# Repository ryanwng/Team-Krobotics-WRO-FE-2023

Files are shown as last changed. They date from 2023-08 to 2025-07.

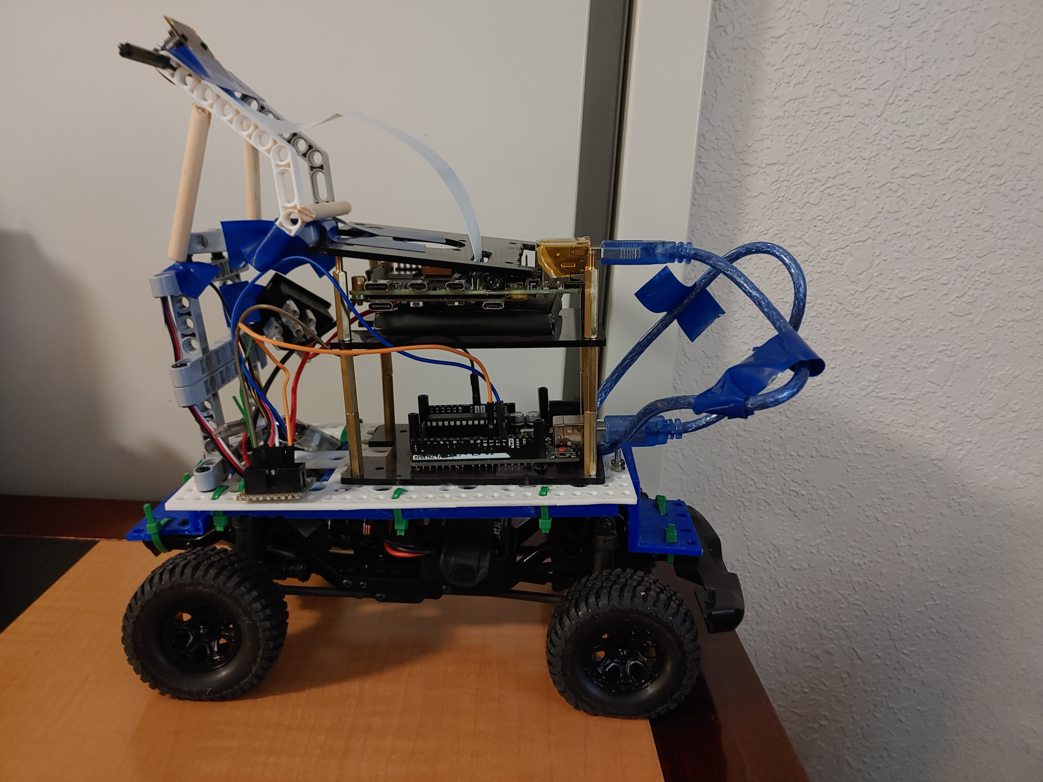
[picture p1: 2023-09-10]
v-photos/Left Side.jpg

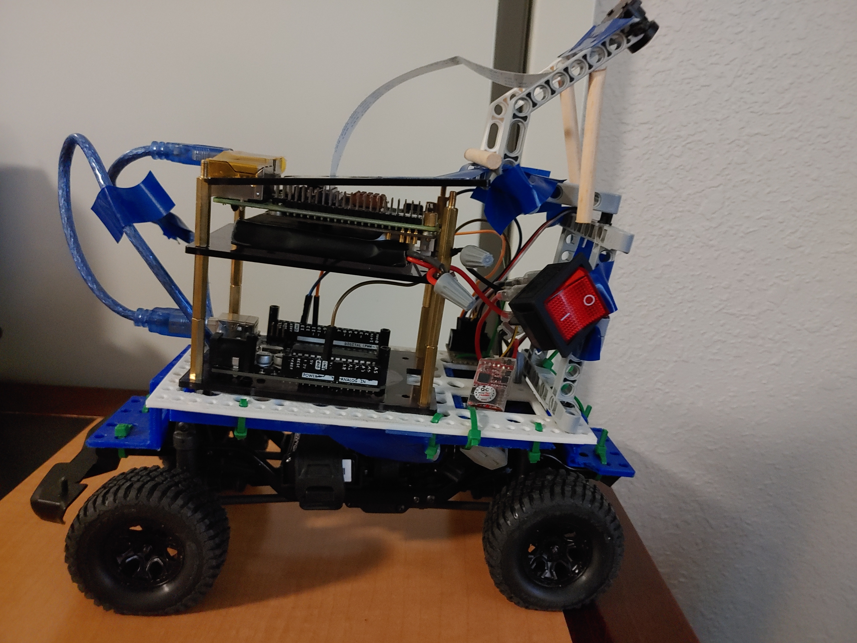
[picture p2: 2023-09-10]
v-photos/Right Side.jpg

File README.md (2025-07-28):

# WRO-FE-2023

# Engineering Documentation | Team Krobotics | Canada
----

This repository contains engineering materials of The Krobot, a vehicle's model from Team Krobotics, for the WRO Future Engineers competition for the 2023 season.

The theme "Connecting the World" focused on exploring how robots can improve shipping logistics and digial infrastuructre to promote safety, sustainability and efficiency. In the Future Engineers category, the competition was to design a self-driving autonomous robot vehicle which was capable of navigating around a randomly generated track with obstacles acting as "traffic lights."

----

## Team Members:

- Kevin Yang - email: kevin.yang.toronto@gmail.com
- Ryan Wang - email: wangryan833@gmail.com

----

## Repository Overview

models - contains 3D printable files for some parts of our robot

schemes - contains a schematic of the the electrical systems

src - contains the code for our robot

t-photos - contains team photos, one serious and one funny

v-photos - contains vehicle photos, from all directions

video - contains youtube links for videos of our robot

----

# Program arrangement and Algorithm Planning
The robot runs on a Raspberry Pi board, we also use an Arducam for Raspberry Pi Camera, OV5647 Pi Camera Module. It detects the surrounding environment including walls and red/green obstacles. The motor and steering servo are both connected to our Arduino Uno board. To count the number of laps, we see how many times the robot detects a low area of ROI one either side (which indicates when it turns). Once it reaches 12, we stop the program after a set amount of time.

When the robot is turned on, it will communicate with the Raspberry Pi, and then waits for a button to be pressed. Once the button is pressed, the servo motor is set to center and the motor speed is set to zero.

**Step 1 - Starting Run:**

We start by accelerating the motor, and begin in the wall-following state. We draw contours and calculate the area of the wall on either side. The difference between the areas is proportional to the distance from the car to the center of the lane.

**Step 2 - Avoiding Walls:**

We run a PID(proportional, integral, derivative) controller to complete the run and avoid the walls. The robot tries to stay in the center of the track by adjusting its position based on the areas of the walls. If the left area is larger, it will correct the error by turning to the right and vice versa. Once the walls’ area on one side is almost nothing, we turn towards that side because it means that it is open and thus we turn in that direction.

**Step 3 - Avoiding Obstacles**

In order to turn correctly for the traffic lights, we have a region of interest at the front of the car which can detect the blocks. We then use HSV values to only capture the blocks, and we find the x and y coordinates of the pillar. Then we adjust to the left and right according to the colour of the pillar, relative to the x-coordinate of the pillar. The y-coordinate of the pillar will dictate how steep of a turn will be needed in order to get to the desired x coordinate, which will in turn mean going around the pillar.

**Step 4 - Counting Laps**

As previously mentioned, the car counts the number of laps by the number of times the car detects lack of area in either left or right ROI. Once it counts that it has turned 12 times, it means that 3 laps have occurred. Then, the program will stop after 8 seconds to ensure it ends in the final area.

----

# Mechanical Parts

**Traxxas Trx4M**

The Traxxas Trx4m was initially chosen due to the fact that it would be easy to modify, as well as being a great all around car which is able to handle all sorts of terrain, electrical components being compatible with ours, as well as fitting the size and weight restraints of the car.

**Raspberry Pi 4 Model B**

The Raspberry Pi was chosen as it is a common computing device which allows for all sorts of coding and intricate use which will be helpful in the competition. Some examples will be communication with the arduino, attaching a camera and powersource, and using the vast amount of libraries that the pi has to offer.

**Arduino Uno R3**

The Arduino was chosen for its popularity and for its great synergy with the Raspberry Pi. Also, it allowed for easy control of the DC motor and the Servo motor, with an easy to understand programming interface and great debugging.

**Furitek Micro Komodo Motor**

The Furitek motor was used over the original Traxxas motor due to the fact that it was brushless versus the latter which was brushed. There are many benefits for using a brushless motor as opposed to a brushed motor. Brushless motors require less power, produce higher speed, and also make less noise.

**Traxxas LiPo Battery and charger**

The battery and charger which powers the DC and Servo motor. The only changes made were connections with the wiring.

**PiSugar S Pro**

The Raspberry Pi Sugar was used to power the Pi, which also ended up powering the Arduino. This would be important in ensuring that both the Pi and Arduino would have sufficient power to run at its full capacity. However, a slight issue occurred as we have two power sources, and the restraints made it such that we could only have one switch to turn both of them on. More will be discussed about this later in the DPST switch section.

**DPST Switch**

Due to the rules, it restricts us to having only one switch to fully turn on the robot. Due to the fact that we have both a power source for the Pi and Arduino, and a power source for the motors, it meant that these two connections had to be connected into one switch. This was done using the DPST switch.

**Mechanical Design**

We decided to use a Traxxas Trx4M as our base, the chassis was expanded on using 3D printed elements and zipties in order to ensure the stability of our parts. For example, our camera is stabilized on a 3D printed mount, which is stabilized through the use of glue and zipties. Our motor is a Furitek Micro Komodo Motor, it has 3 wires that connect to our esc to control speed and torque. This motor is directly compatible with the car we picked. Using cases and bases to hold the Raspberry Pi and its respective power source was helpful in condensing the robot in size. Lego was also used to create a camera stand to ensure that the camera would face down. Finally, tape was used in some areas, along with hot glue to increase the stability of the car in weaker areas.

**3D Parts**

A base was designed in order to hold the Raspberry Pi, Arduino, wiring and some other pieces. A camera stand was previously designed to ensure that the camera would stay in the same place and be stable while driving. However, it was figured later on that the camera wouldn't be able to face down, and so the stand was made with lego and some wooden pieces to ensure it would stay in place. 

**Hardware Issues**

There ended up being some hardware issues which he had to fix throughout the preparation of the competition. Firstly, the use of the button on the Pi Sugar S Pro was necessary in order to fulfill the requirements of the competition of using only one button to start the program. This meant adding additional code, along with solidfying the reason for using the Pi Sugar S Pro compared to other power sources, such as lithium batteries. Also, for the Raspberry Pi it would be necessary to code a way to run a program immediately upon turning on. This was done using the command "sudo crontab -e" which allows for programs to run upon rebooting of the raspberry pi. This alongside with the GPIO button on the Pi Sugar S pro was invaluable in allowing for a suitable car which can perform all its necessary functions.

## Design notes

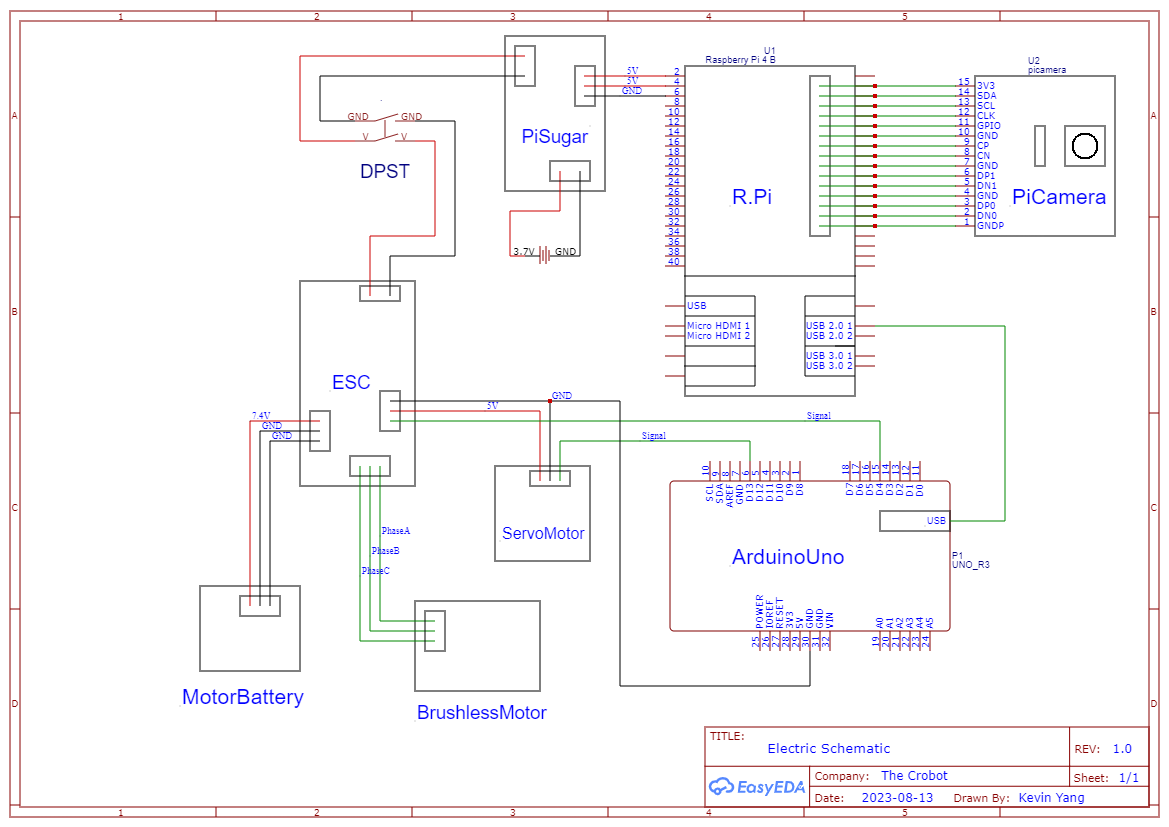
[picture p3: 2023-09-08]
schemes/Updated Electric Schematic.png

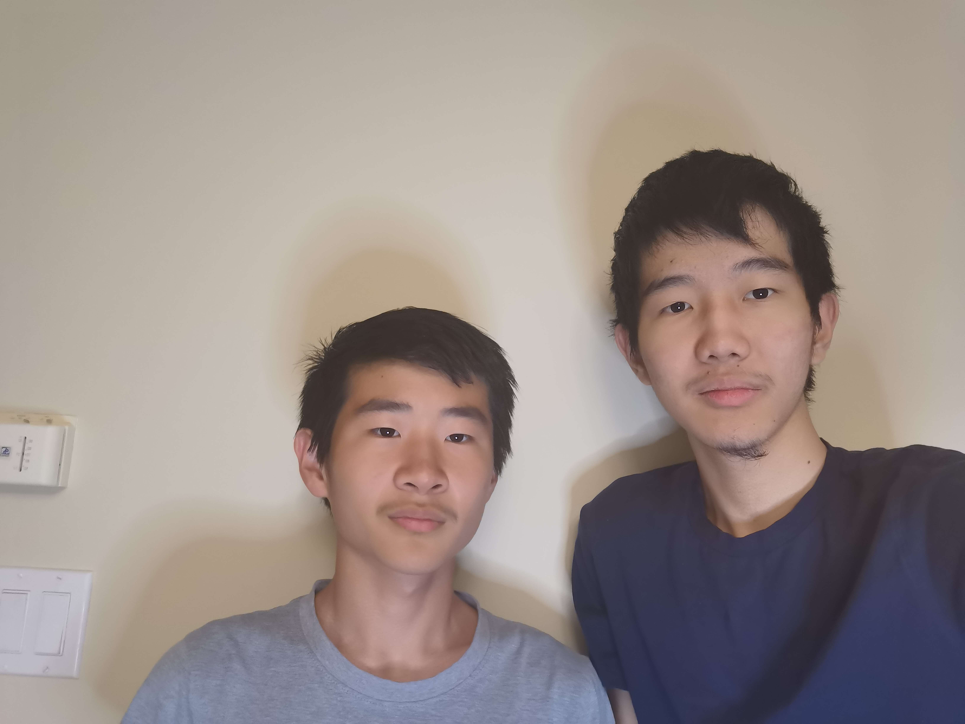
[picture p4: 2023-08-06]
t-photos/TeamPhoto.jpg

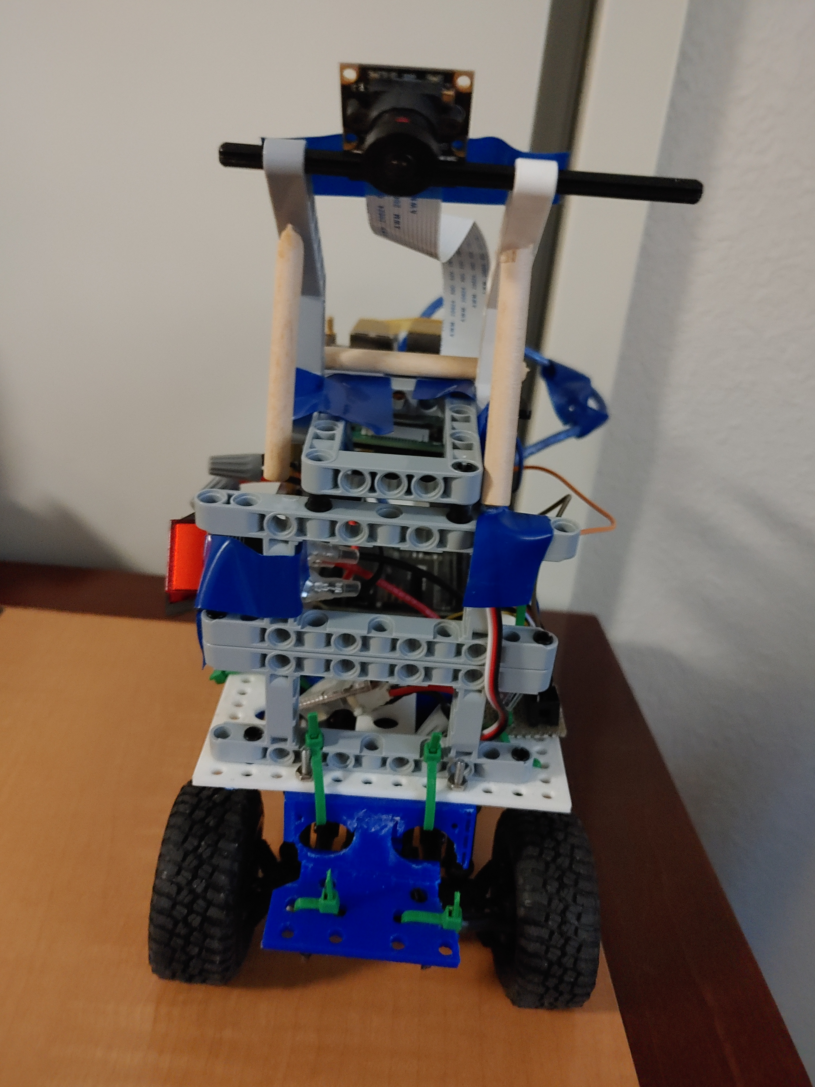
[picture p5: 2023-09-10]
v-photos/Front Side.jpg

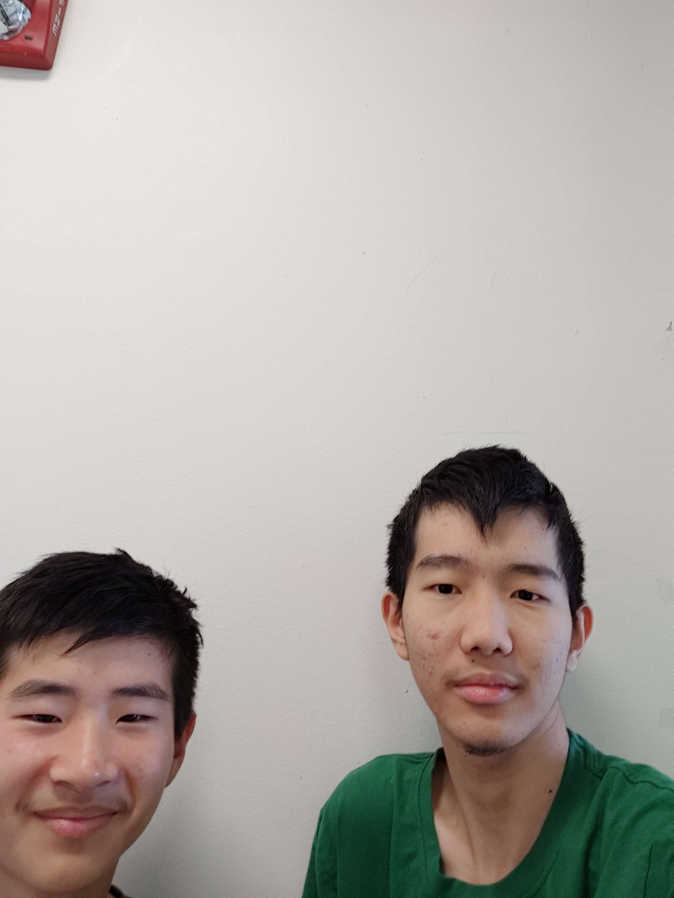
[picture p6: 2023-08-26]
t-photos/funny team photo.jpg

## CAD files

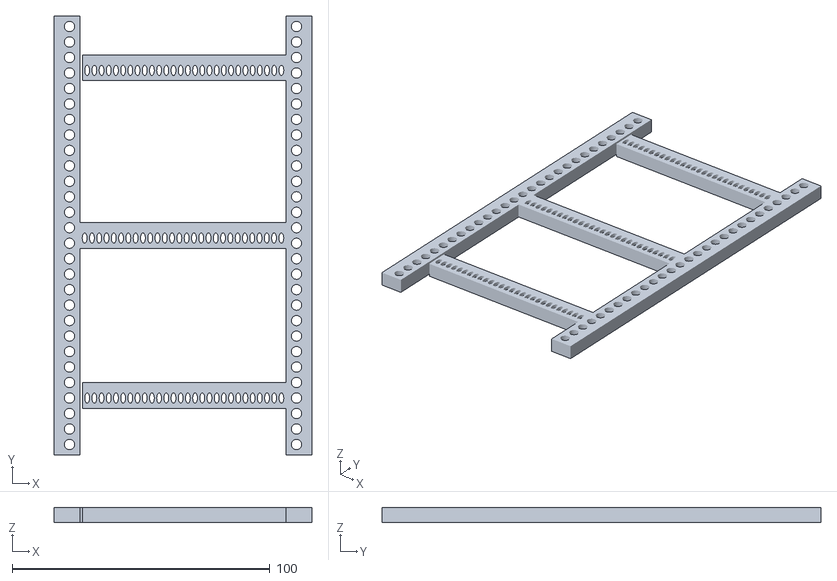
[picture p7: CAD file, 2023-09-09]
models/Bottom Chassis Support.stl
100.0 x 170.0 x 6.00

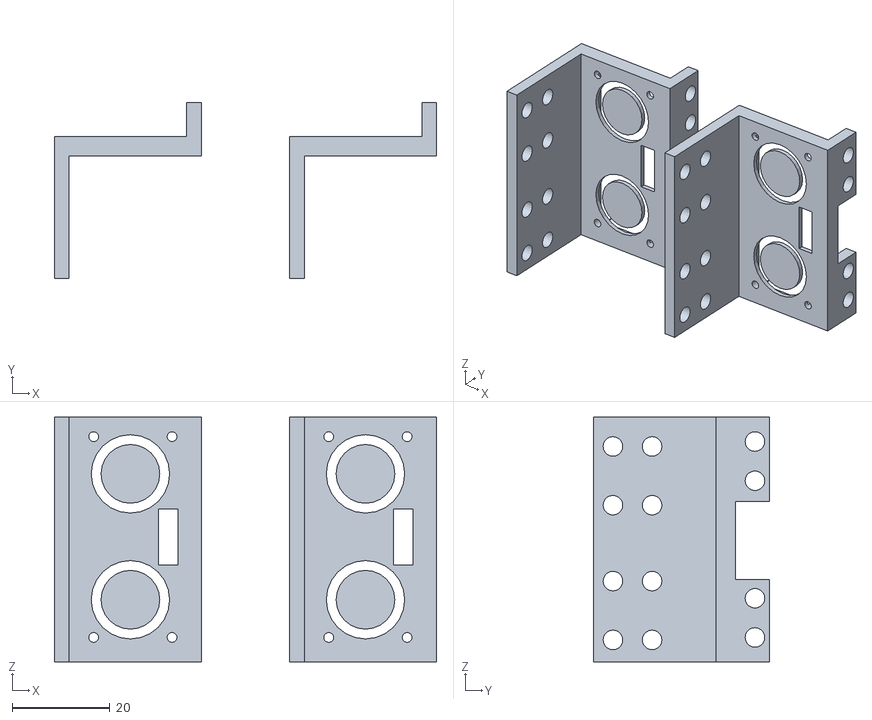
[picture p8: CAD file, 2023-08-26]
models/Chassis Axis Support.stl
78.0 x 36.0 x 50.0

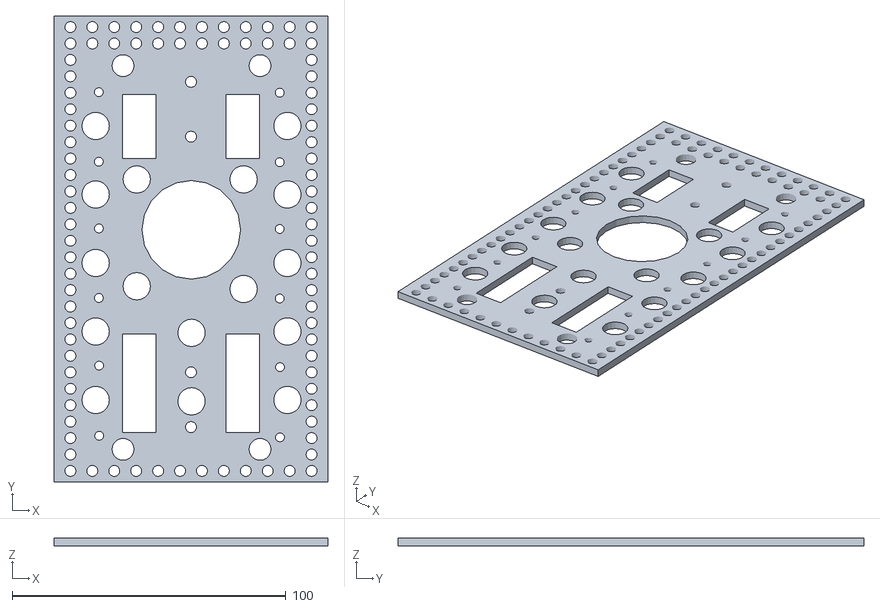
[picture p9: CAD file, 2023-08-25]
models/Chassis.stl
100.0 x 170.0 x 3.00

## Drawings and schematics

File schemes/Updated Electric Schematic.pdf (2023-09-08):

# R.Pi

# PiCamera

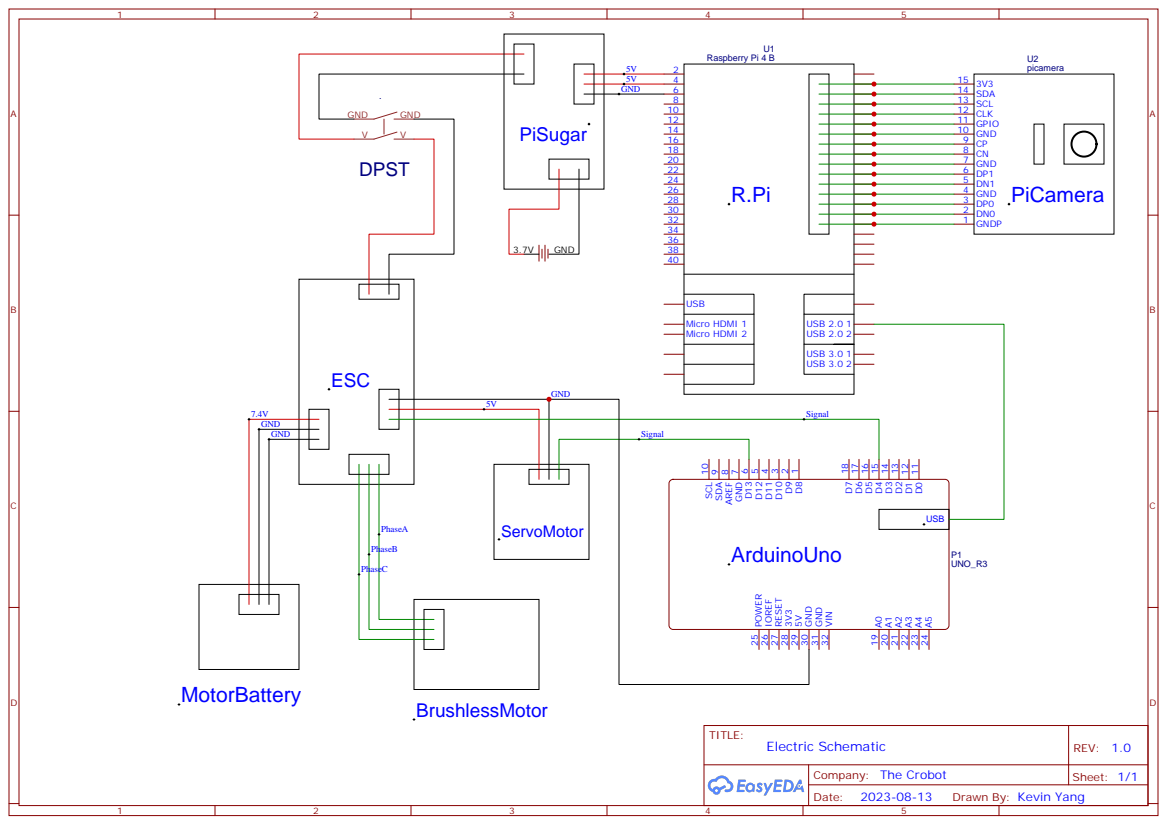
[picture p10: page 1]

Drawn By: Kevin Yang

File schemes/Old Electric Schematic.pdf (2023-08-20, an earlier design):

# RPi

# PiCamera

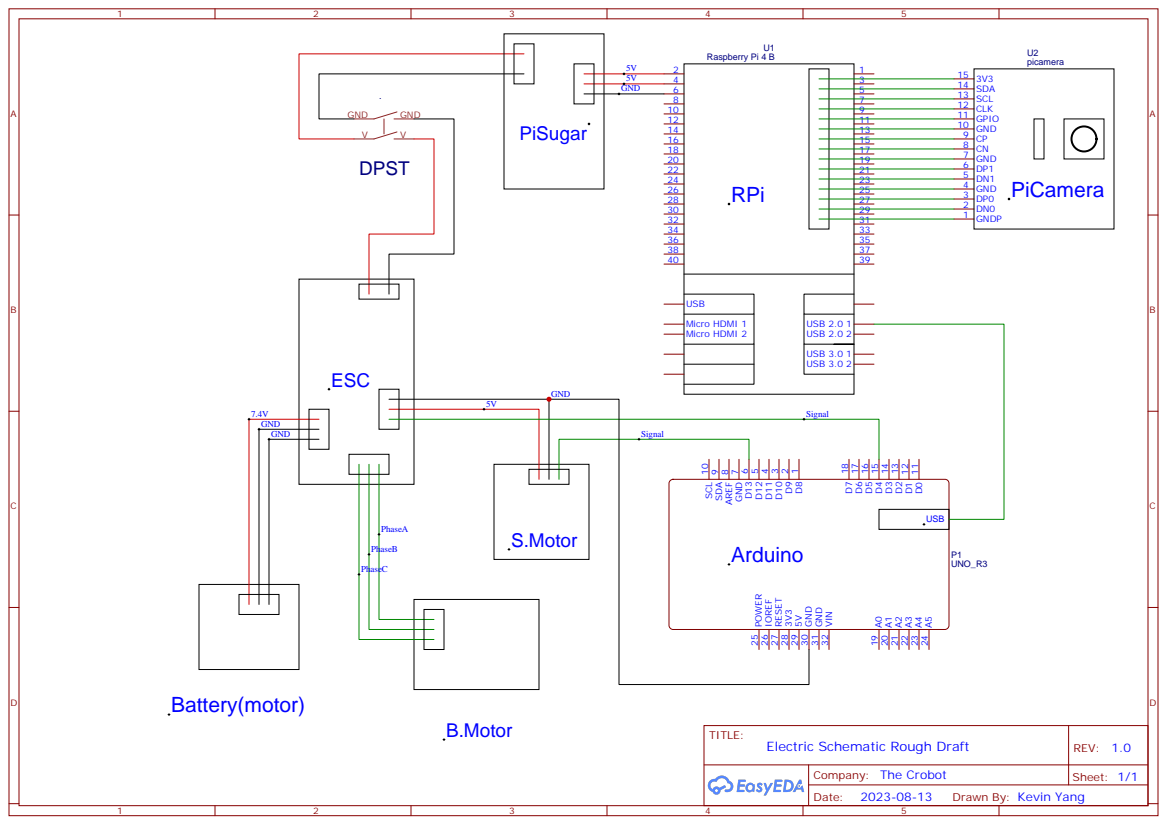
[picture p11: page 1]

Drawn By: Kevin Yang

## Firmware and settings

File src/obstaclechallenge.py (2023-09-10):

'''
This code can successfully do the obstacle challenge.

'''

import cv2
import time
import numpy as np
from picamera2 import Picamera2
import serial
#import RPi.GPIO as GPIO

if __name__ == '__main__':

    
    This part will allow the code to run at the start of a button instead of running it manually.
    GPIO.setwarnings(False)
    GPIO.setmode(GPIO.BOARD)
    GPIO.setup(5, GPIO.IN, pull_up_down=GPIO.PUD_UP)

    
        while(True):
        if GPIO.input(5) == GPIO.LOW: #wait for button to be pressed
            break
    

    #Intializing the camera
    picam2 = Picamera2()
    picam2.preview_configuration.main.size = (640,480)
    picam2.preview_configuration.main.format = "RGB888"
    picam2.preview_configuration.align()
    picam2.configure("preview")
    picam2.start()

    #Initalizing variables
    width = 640
    height = 480
    kp = 0.006
    angle = 2090
    turns = 0
    pid = True
    red = False
    green = False
    

    # Initialize last detection time
    last_detection_time = time.time()
    delay = time.time()

    #Region of interests
    lft = [[0,150],[150,480]]
    right = [[490,150],[640,480]]
    mid = [[150, 150], [490, 480]]
    lowmid = [[0,300], [640, 480]]
    points = [(0,0),(640,0),(640,480),(0,480)]
    
    steering = 0
    redarea = 0
    greenarea = 0
    change = False
    lap = False

    blueColor = (255,0,0) # Blue
    greenColor = (0,255,0) #green
    midRectColor = (0,0,255) #Red!
    lftRectColor = (255,0,0) # Blue
    rtRectColor = (255,0,0)
    midRectColor = (0,0,255) #Red!
    greenColor = (0,255,0) #hmm, I wonder what colour this is

    lower_red = np.array([120, 140, 90]) #([120, 30, 90])
    upper_red = np.array([180, 255, 255]) #([180, 255, 255]) 
    lower_green = np.array([30, 80, 30]) #([60, 100, 30])
    upper_green = np.array([100, 255, 255]) #([90, 255, 255])

    ser = serial.Serial('/dev/ttyACM0', 115200, timeout = 1) #approximately 115200 characters per second
    ser.flush()
    time.sleep(8)	    
    
    speed = 1680 #faster speed to accelerate
    ser.write((str(speed) + "\n").encode('utf-8'))

    while True:
        steering = 1
        im = picam2.capture_array()


        input = np.float32(points)
        output = np.float32([(0,0), (width-1, 0), (width-1,height-1), (0, height-1)])

        matrix = cv2.getPerspectiveTransform(input,output)
        imgPerspective = cv2.warpPerspective(im, matrix, (width, height),
                                            cv2.INTER_LINEAR, borderMode=cv2.BORDER_CONSTANT, borderValue=(0,0,0))
                                            
                                                          
	# Define range for HSV
        hsv = cv2.cvtColor(im, cv2.COLOR_BGR2HSV)
            
        #Red Detection Begins ~
        max_area = 0
        max_cnt = None
        
        rmask = cv2.inRange(hsv, lower_red, upper_red) #test to see if it can be taken out of while loop

        contours_red, _ = cv2.findContours(rmask, cv2.RETR_TREE, cv2.CHAIN_APPROX_SIMPLE)

        for i in range(len(contours_red)):
            cnt = contours_red[i]
            redarea = cv2.contourArea(cnt)
            if redarea > max_area:
                max_area = redarea
                max_cnt = cnt
            if(redarea > 1500 and max_cnt is not None):
                cv2.drawContours(im, contours_red, i, (0, 255, 0), 2)
                M = cv2.moments(max_cnt)

                # Calculate x,y coordinate of center
                cX = int(M["m10"] / M["m00"])
                cY = int(M["m01"] / M["m00"])

                print("Red Centroid coordinates: ", cX,",",cY)

                # Draw contour and center of shape on image
                cv2.drawContours(im, [max_cnt], -1, (0, 255, 0), 3)
                cv2.circle(im,(cX,cY),5,(255,255,255),-1)
                
                if cX > 170:
                #constants may be changed
                    steering = 0.05*(cX-200) + 0.1*(cY)
                    if steering > 45:
                        steering = 45
                
                elif cX < 170 and cX > 50: #doesn't need to readjust 
                    steering = 0
               
                elif cX < 50: #Helps with edge cases
                    steering = -35
                
                
                angle = 2090 + steering
                red = True
                green = False
                pid = False
            else:
                pid = True

        
        #Green detection begins ~
        
        if red == False:
            max_area = 0
            max_cnt = None
       
            gmask = cv2.inRange(hsv, lower_green, upper_green)
            contours_green, _ = cv2.findContours(gmask, cv2.RETR_TREE, cv2.CHAIN_APPROX_SIMPLE)
			
            for i in range(len(contours_green)):
                cnt = contours_green[i]
                greenarea = cv2.contourArea(cnt)
                if greenarea > max_area:
	                max_area = greenarea
	                max_cnt = cnt
                if(greenarea > 1500 and max_cnt is not None):
                    cv2.drawContours(im, contours_green, i, (0, 255, 0), 2)
                    M = cv2.moments(cnt)

		    # Calculate x,y coordinate of center
                    cX = int(M["m10"] / M["m00"])
                    cY = int(M["m01"] / M["m00"])

                    print("Green Centroid coordinates: ", cX,",",cY)

		# Draw contour and center of shape on image
                    cv2.drawContours(im, [cnt], -1, (0, 255, 0), 3)
                    cv2.circle(im,(cX,cY),5,(255,255,255),-1)
					
                    if cX < 480:
			#constants may be changed
                        steering = -0.05*(cX-200) - 0.1*(cY)
                        if steering < -45:
                            steering = -45
					
                    elif cX > 480 and cX < 550: #doesn't need to readjust 
                        steering = 0
                    
                    elif cX > 550:
                        steering = 35
					
                    angle = 2090 + steering
                    green = True
                    red = False
                    pid = False
                else:
                    pid = True       
            

	
      

        # Find contours in the edge image
        imgGray = cv2.cvtColor(imgPerspective, cv2.COLOR_BGR2GRAY)
        ret, imgThresh = cv2.threshold(imgGray, 35, 255, cv2.THRESH_BINARY_INV) #This number may be subject to change, in order to detect only black
        # First coord is top left, second coord is bottom right.

        contoursLeft, _ = cv2.findContours(imgThresh[lft[0][1]:lft[1][1],lft[0][0]:lft[1][0]], cv2.RETR_EXTERNAL, cv2.CHAIN_APPROX_SIMPLE)
        contoursRight, _ = cv2.findContours(imgThresh[right[0][1]:right[1][1],right[0][0]:right[1][0]], cv2.RETR_EXTERNAL, cv2.CHAIN_APPROX_SIMPLE)
        contoursLowMid, _ = cv2.findContours(imgThresh[lowmid[0][1]:lowmid[1][1],lowmid[0][0]:lowmid[1][0]], cv2.RETR_EXTERNAL, cv2.CHAIN_APPROX_SIMPLE)
        
        # Offset based off topleft corner of each left/right rectrangle
        contoursLeft = [ c + lft[0] for c in contoursLeft]
        contoursRight = [ c + right[0] for c in contoursRight]
        contoursLowMid = [ c + lowmid[0] for c in contoursLowMid]

        # Draw contours on the original image
        cv2.drawContours(im, contoursLeft, -1, (0, 255, 0), 2)
        cv2.drawContours(im, contoursRight, -1, (0, 255, 0), 2)
        #cv2.drawContours(im, contoursLowMid, -1 (0, 255, 0), 2)

       
        lftTot = 0
        for c in contoursLeft:
            lftTot += cv2.contourArea(c)

        rtTot = 0
        for c in contoursRight:
            rtTot += cv2.contourArea(c)    

        lowMidTot = 0
        for c in contoursLowMid:
            lowMidTot += cv2.contourArea(c)   

        if angle > 2180 or angle < 2000:
                angle = 2090 

        if((lftTot < 2000 or rtTot < 2000) and time.time() - delay >= 8.5):
	        turns += 1
	        delay = time.time()
	        
        if pid == True:
            red = False
            green = False
            error = lftTot-rtTot
            if steering == 1:
                steering = kp * error
                #print("Wall PID")
                if error > 450 or error < -450:
                    angle = 2090 + steering
                if lowMidTot > 25000:
                    if lftTot < rtTot:
                        steering = 45
                    elif rtTot > lftTot:
                        steering = -45
            steering = int(steering)
            
        '''
        if turns == 8:
            if change == False:
                delayer = time.time()
                change = True
                check = False
            if (red == True and time.time() -  delayer >= 1) and check == False: #implies needs to finish last lap counterclockwise
                print("Start")
                check = True
                ser.flush()
                speed = 1675
                if lftTot > rtTot:
                    angle = 2120
                elif rtTot < lftTot:
                    angle = 2060
                ser.write((str(speed) + "\n").encode('utf-8'))
                ser.write((str(angle) + "\n").encode('utf-8'))
                time.sleep(3)
                ser.flush()
                
                
                if lftTot > rtTot:
                    angle = 2030
                    ser.write((str(angle) + "\n").encode('utf-8'))
                    time.sleep(5)
                    print("End")
                elif rtTot > lftTot:
                    angle = 2150
                    ser.write((str(angle) + "\n").encode('utf-8'))
                    time.sleep(5)
                    print("End")
                    '''
                
        if turns >=12: 
            if lap == False:
                last_detection_time = time.time() 
                lap = True
            if (time.time() - last_detection_time >= 7.5):
                ser.flush()
                speed = 1500
                angle = 2090
                ser.write((str(speed) + "\n").encode('utf-8'))
                ser.write((str(angle) + "\n").encode('utf-8'))
                break
                cv2.destroyAllWindows()
        
        angle = int(angle)    
        if angle > 2140:
            angle = 2140
        elif angle < 2040:
            angle = 2040
       
        #print("Angle:",angle)
        #print("Steering:",steering)
        #print("Red Area:", redarea)
        #print("Green Area:", greenarea)
        #print("Error:",error)
        #print("Turns:", turns)
        #print("Orange turns:",orangeturns)
        #print("Lowmid total:", lowMidTot)
        #print(red)
    
        ser.write((str(angle) + "\n").encode('utf-8'))
        
	'''
        cv2.rectangle(im,tuple(lft[0]),tuple(lft[1]),lftRectColor,2)
        cv2.rectangle(im,tuple(right[0]),tuple(right[1]),rtRectColor,2)
        cv2.rectangle(im,tuple(mid[0]),tuple(mid[1]), midRectColor,2)
        cv2.rectangle(im,tuple(lowmid[0]),tuple(lowmid[1]), greenColor,2)
        cv2.putText(im,str(lftTot),(lft[0][0],lft[0][1]-5),cv2.FONT_HERSHEY_SIMPLEX,1,lftRectColor,2,cv2.LINE_AA)
        cv2.putText(im,str(rtTot),(right[0][0],right[0][1]-5),cv2.FONT_HERSHEY_SIMPLEX,1,rtRectColor,2,cv2.LINE_AA)
        cv2.putText(im,str(angle),(lft[0][0]-20,right[0][1]-50),cv2.FONT_HERSHEY_SIMPLEX,1,lftRectColor,2,cv2.LINE_AA)
        cv2.putText(im,str(turns),(lft[0][0]-50,right[0][1]-50),cv2.FONT_HERSHEY_SIMPLEX,1,lftRectColor,2,cv2.LINE_AA)
        cv2.putText(im,str(greenarea),(mid[0][0]-20,mid[0][1]-50),cv2.FONT_HERSHEY_SIMPLEX,1,greenColor,2,cv2.LINE_AA) #Area of green contours
        cv2.putText(im,str(redarea),(mid[0][0]-20,mid[0][1]-100),cv2.FONT_HERSHEY_SIMPLEX,1,midRectColor,2,cv2.LINE_AA) #Area of red contours
        cv2.imshow("Final", im)

        if cv2.waitKey(1)==ord('q'): #End program, press 'q'
            ser.flush()
            speed = 1500
            angle = 2090
            ser.write((str(speed) + "\n").encode('utf-8'))
            ser.write((str(angle) + "\n").encode('utf-8'))
            break
    cv2.destroyAllWindows()
    '''

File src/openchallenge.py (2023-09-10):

'''
This code can successfully do the open challenge.


'''
import cv2
import time
import numpy as np
from picamera2 import Picamera2
import serial
import RPi.GPIO as GPIO

if __name__ == '__main__':
    

    #Initializing the camera
    picam2 = Picamera2()
    picam2.preview_configuration.main.size = (640,480)
    picam2.preview_configuration.main.format = "RGB888"
    picam2.preview_configuration.align()
    picam2.configure("preview")
    picam2.start()

    #Initalizing variables
    width = 640
    height = 480
    kp = 0.008
    angle = 2090
    turns = 0

    # Initializing last detection time
    last_detection_time = time.time()
    delay = time.time()

    #Region of interests for walls 
    lft = [[0,150],[150,480]]
    right = [[490,150],[640,480]]

    blueColour = (255,0,0) # Blue

    # Define range for blue and orange in HSV
    lower_blue = np.array([100,40,40])
    upper_blue = np.array([180,255,255])
	
    lower_orange = np.array([0,40,20])
    upper_orange = np.array([11,255,255])

	
    # Whole screen
    points = [(0,0),(640,0),(640,480),(0,480)]
    
    ser = serial.Serial('/dev/ttyACM0', 115200, timeout = 1) #approximately 115200 characters per second
    ser.flush()
    time.sleep(8)	    
    
    GPIO.setwarnings(False)
    GPIO.setmode(GPIO.BOARD)
    GPIO.setup(5, GPIO.IN, pull_up_down=GPIO.PUD_UP)
	
    while(True):
        if GPIO.input(5) == GPIO.LOW: #Waits for a button to be pressed before running the code
            break
            
    speed = 1660
    ser.write((str(speed) + "\n").encode('utf-8'))
    
    while True:
        im= picam2.capture_array()


        input = np.float32(points)
        output = np.float32([(0,0), (width-1, 0), (width-1,height-1), (0, height-1)])

        matrix = cv2.getPerspectiveTransform(input,output)
        imgPerspective = cv2.warpPerspective(im, matrix, (width, height),
                                            cv2.INTER_LINEAR, borderMode=cv2.BORDER_CONSTANT, borderValue=(0,0,0))
                                            
                                                          
	# Range for hsv
        hsv = cv2.cvtColor(im, cv2.COLOR_BGR2HSV)

        # Threshold the HSV image to get only blue and orange colors
        mask_blue = cv2.inRange(hsv, lower_blue, upper_blue)
        mask_orange = cv2.inRange(hsv, lower_orange, upper_orange)

        # Bitwise-OR mask and original image
        res_blue = cv2.bitwise_and(im,im, mask= mask_blue)
        res_orange = cv2.bitwise_and(im,im, mask= mask_orange)

        # Find contours in the images
        contours_blue, _ = cv2.findContours(mask_blue, cv2.RETR_TREE, cv2.CHAIN_APPROX_SIMPLE)
        contours_orange, _ = cv2.findContours(mask_orange, cv2.RETR_TREE, cv2.CHAIN_APPROX_SIMPLE)

	# Find area of blue and orange lines respectively.
        for i in range(len(contours_blue)):
            cnt = contours_blue[i]
            areablue = cv2.contourArea(cnt)
            
        for i in range(len(contours_orange)):
            cnt = contours_orange[i]
            areaorang = cv2.contourArea(cnt)
    

        # Find contours in the edge image
        imgGray = cv2.cvtColor(imgPerspective, cv2.COLOR_BGR2GRAY)
        ret, imgThresh = cv2.threshold(imgGray, 40, 255, cv2.THRESH_BINARY_INV) #1st number (40) may be subject to change, in order to detect only black depending on lighting

	    
        # First coord is top left, second coord is bottom right.

        contoursLeft, _ = cv2.findContours(imgThresh[lft[0][1]:lft[1][1],lft[0][0]:lft[1][0]], cv2.RETR_EXTERNAL, cv2.CHAIN_APPROX_SIMPLE)
        contoursRight, _ = cv2.findContours(imgThresh[right[0][1]:right[1][1],right[0][0]:right[1][0]], cv2.RETR_EXTERNAL, cv2.CHAIN_APPROX_SIMPLE)
        
        
        # Offset based off topleft corner of each left/right rectrangle
        contoursLeft = [ c + lft[0] for c in contoursLeft]
        contoursRight = [ c + right[0] for c in contoursRight]
        

	# Finding area of black in left and right Region of Interests (ROI)
        lftTot = 0
        for c in contoursLeft:
            lftTot += cv2.contourArea(c)

        rtTot = 0
        for c in contoursRight:
            rtTot += cv2.contourArea(c)
                   

	# Steering logic
        error = lftTot-rtTot
        steering = kp * error
        steering = int(steering)

	# If angle is too wide, car goes back to 2090    
        if angle > 2180 or angle < 2000:
            angle = 2090

	# If there's enough disparity between the areas of the two ROIS, enact steering logic
	if error > 450 or error < -450:
            angle = 2090 + steering
		
    	# Counts the number of turns done, with a delay on counting the number of laps
        if ((lftTot < 2000 or rtTot < 2000) and time.time() - delay >= 8.5):
            turns += 1
            delay = time.time()     

	# If 12 turns have elapsed (3 laps), then delay for a little bit, before stopping
        if turns >=12: 
            if lap == False:
                last_detection_time = time.time()
            lap = True
            if (time.time() - last_detection_time >= 6):
                ser.flush()
                speed = 1500
                angle = 2090
                ser.write((str(speed) + "\n").encode('utf-8'))
                ser.write((str(angle) + "\n").encode('utf-8'))
                break
                cv2.destroyAllWindows()
				
        #Makes sure the angle is not too extreme
        angle = int(angle)    
        if angle > 2140:
            angle = 2160
        elif angle < 2040:
            angle = 2040
    
        ser.write((str(angle) + "\n").encode('utf-8'))

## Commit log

2023-06-18 Camera code, proportional wall
    The mostly final code for the camera, and the start of trying to do the open challenge with the proportional wall technique
2023-06-29 Update finaledge.py
    Camera detects edges, turns but turns the wrong way sometimes. More clarity, some safety, and a little optimizatione
2023-08-20 current photos of the car
2023-08-26 Rename ArduinoCode.ino to Arduino(open and obstacle).ino
    naming
2023-08-27 Delete 3d Camera Frame.stl
    Not used in design of car anymore
    [3d Camera Frame.stl]
2023-08-29 Update ArduinoCode(open and obstacle).ino
    Formatting, cleaning up code
2023-09-04 Update ArduinoCode(open and obstacle).ino
    Allows for car to go backwards faster
2023-09-08 Update and rename ArduinoCode(open and obstacle).ino to Arduino (open and obstacle).ino
    some minor edits
2023-09-08 Add files via upload
    update schematic
2023-09-09 Delete models/Chassis Support (Ultrasonic Sensor holder).stl
    Will be replaced
    [Chassis Support (Ultrasonic Sensor holder).stl]
